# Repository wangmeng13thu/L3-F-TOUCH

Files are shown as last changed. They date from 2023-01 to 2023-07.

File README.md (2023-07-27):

L3 F-TOUCH Design
=================

<p align="center">
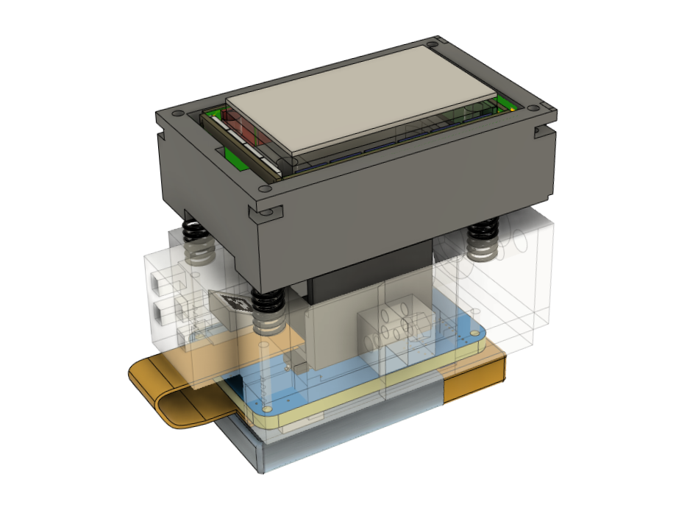
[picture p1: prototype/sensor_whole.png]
  
</p>

L3 F-TOUCH sensor is an enhanced version of the GelSight sensor, it acquires a much better three-axis force sensing capability while being ***L***ight-weight, ***L***ow-cost and wire***L***ess for the ease of replication and deployment.

We decouple the three-axis force and tactile information using a suspension structure with mirrored visual tag. The L3 F-TOUCH demonstrates an improved force sensing capability immuned from contact geometry compared to other GelSight-like designs while being light and cost-effective compared to commercial three-axis force sensors. The wireless data transmission feature also enables broader applications of akin vision-based tactile sensors. 

This repository contains the documentation and manufacturing files for L3 F-TOUCH tactile sensor.

Manufacturing
-------------

* The 3D design files and BOM are in [prototype](prototype/);
* The wireless camera module design is in [PCB](PCB/);

Running
-----------

* Compile and upload the [firmware](/firmware) via [PlatformIO](https://github.com/platformio/platformio-vscode-ide) (WiFi must be configured);
* Use [VLC](https://github.com/videolan/vlc) to check the RTSP video streaming. Adress can be found in Serial monitor when startup.
* Run [L3-FTOUCH.py](/software/L3-FTOUCH.py) for demonstration;

Remarks
-----------
* Modify the firmware to use picture mode for higher quality images (advanced).

Video
-----------

L3 F-TOUCH: A Wireless GelSight with Decoupled Tactile and Three-axis Force Sensing (https://www.youtube.com/watch?v=NIsbJhs_ChQ "L3 F-TOUCH: A Wireless GelSight with Decoupled Tactile and Three-axis Force Sensing")

Citation
-----------
If you use this project in your research, please cite:

```BibTeX
@article{li20233,
  title={L$^3$ F-TOUCH: A Wireless GelSight with Decoupled Tactile and Three-axis Force Sensing},
  author={Li, Wanlin and Wang, Meng and Li, Jiarui and Su, Yao and Jha, Devesh K and Qian, Xinyuan and Althoefer, Kaspar and Liu, Hangxin},
  journal={IEEE Robotics and Automation Letters},
  volume={8},
  number={8},
  pages={5148--5155},
  year={2023},
  publisher={IEEE}
}
```

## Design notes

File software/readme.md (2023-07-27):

<p align="left">
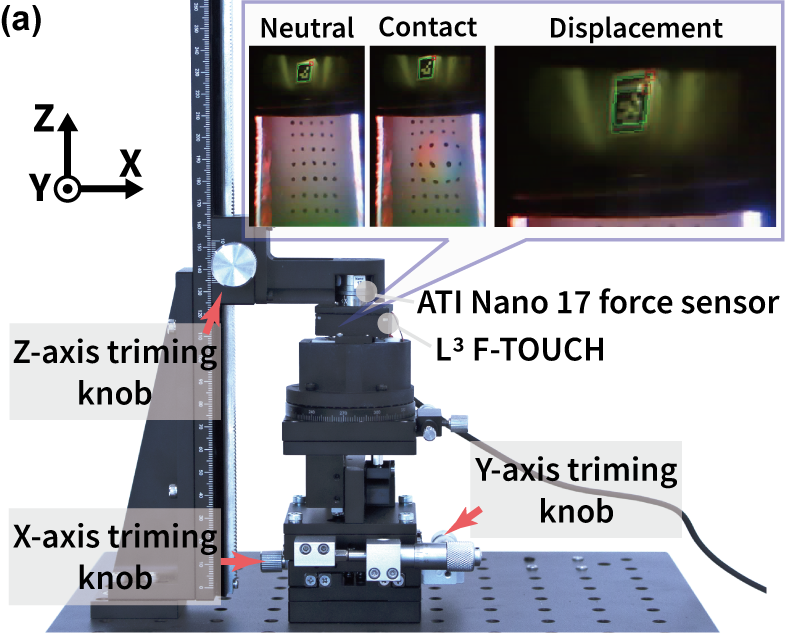
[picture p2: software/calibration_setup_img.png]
  
</p>

* For the Tactile Mode, you can use any vision-based tactile sensor (VBTS) technique, for instance, GelSight, GelSlim etc.
* For the Force Mode, you can also use any AR tag. Here we use ArUco marker and collected the groundtruth data from the ATI F/T sensor and the L3-FTOUCH sensor data using the setup shown above. Please make sure that the two data are synchronized and saved, for instance, in a csv file. Then run ForceCalibration3by3.py to generate the calibration matrix forcematrix.npy. An example of the predicted data is presented in Linearity.mat. The complete version with user interface is L3-FTOUCH.py.

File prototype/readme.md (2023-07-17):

This page is for the sensor's prototype components:

* files with .stl are 3D printed sensor sturctures. The Top is connected to the Bottom1 and Bottom2 via springs, while Bottom1 and Bottom2 are connected via bolts.

* The SMD LEDs used are LUXEON 2835 Color Line. The PCB of the LEDs are in [PCB](../PCB/) folder.

* The Marker used is ArUco Marker 4x4(50) which can be generated from [here](https://chev.me/arucogen/).

* The BOM is as follows:
<p align="left">
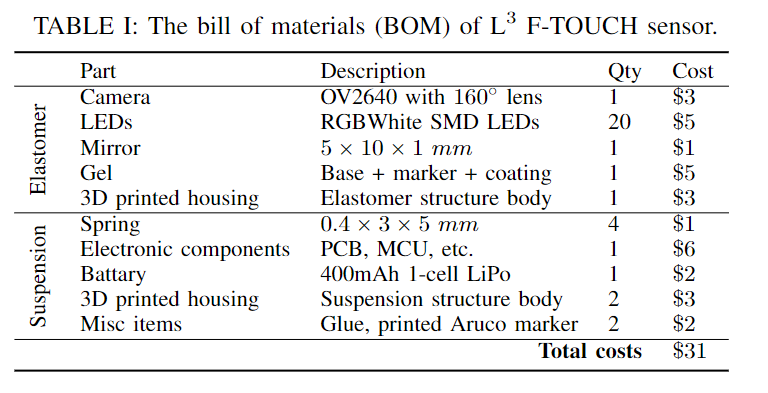
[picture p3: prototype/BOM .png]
  
</p>

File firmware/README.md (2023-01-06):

# GelSightRTSP

This repository is based on [ESP32-CAM RTSP stream](https://github.com/circuitrocks/ESP32-RTSP), with more functions added and optimized for GelSight sensors. 

## Compiling with PlatformIO
Just open the folder containing the files with PlatformIO and adjust your settings in platformio.ini. Required libraries are either automatically installed or in the lib folder.

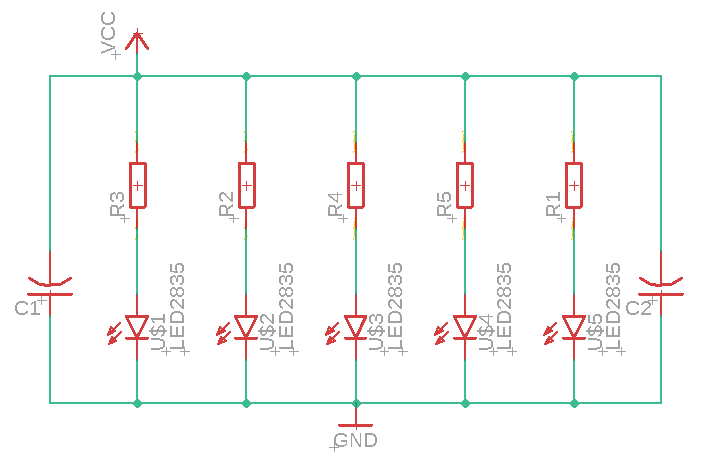
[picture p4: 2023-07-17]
PCB/PCB_Schematic.png

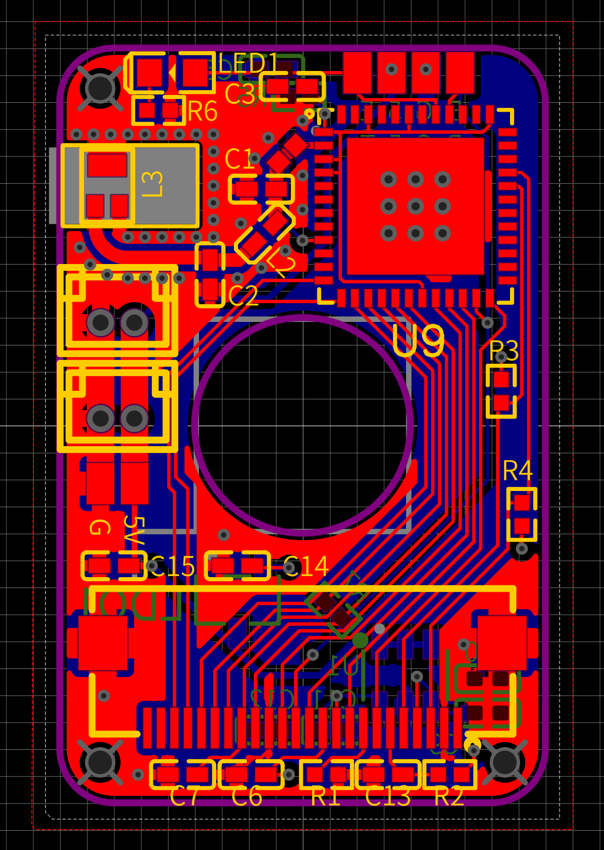
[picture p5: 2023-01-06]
PCB/pcb.png

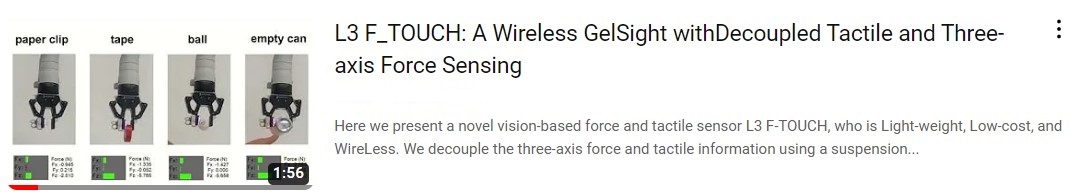
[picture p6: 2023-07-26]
prototype/YouTube.jpg

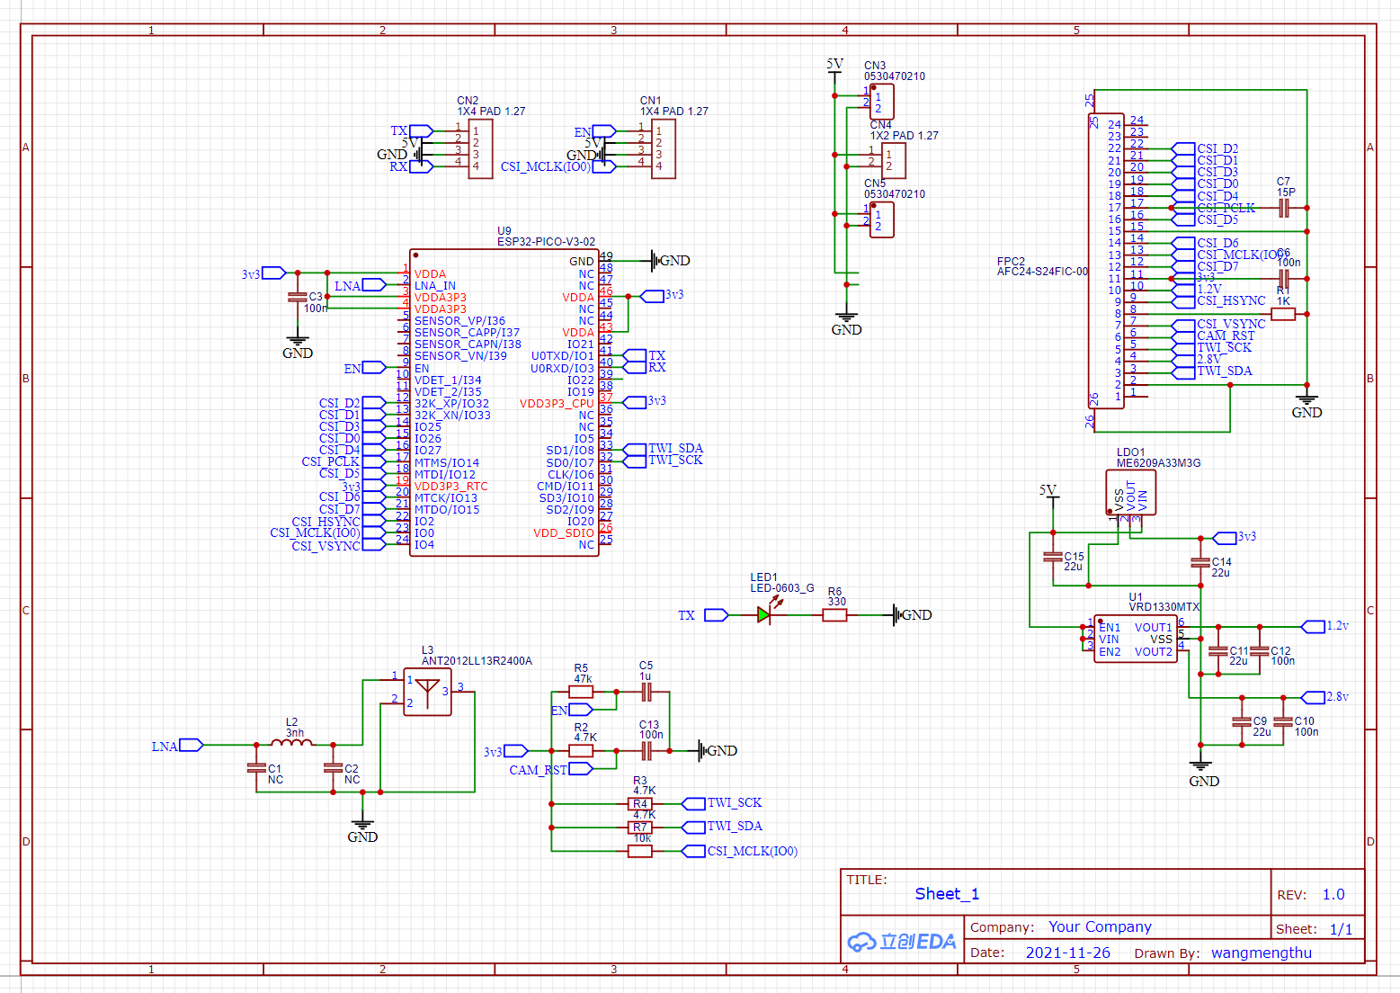
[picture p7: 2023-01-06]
PCB/scheme.png

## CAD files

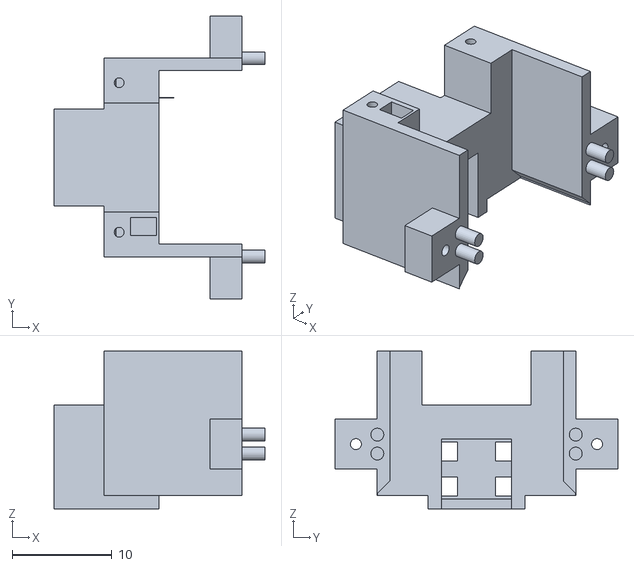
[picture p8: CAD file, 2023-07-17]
prototype/Bottom1.stl
21.1 x 28.4 x 15.8

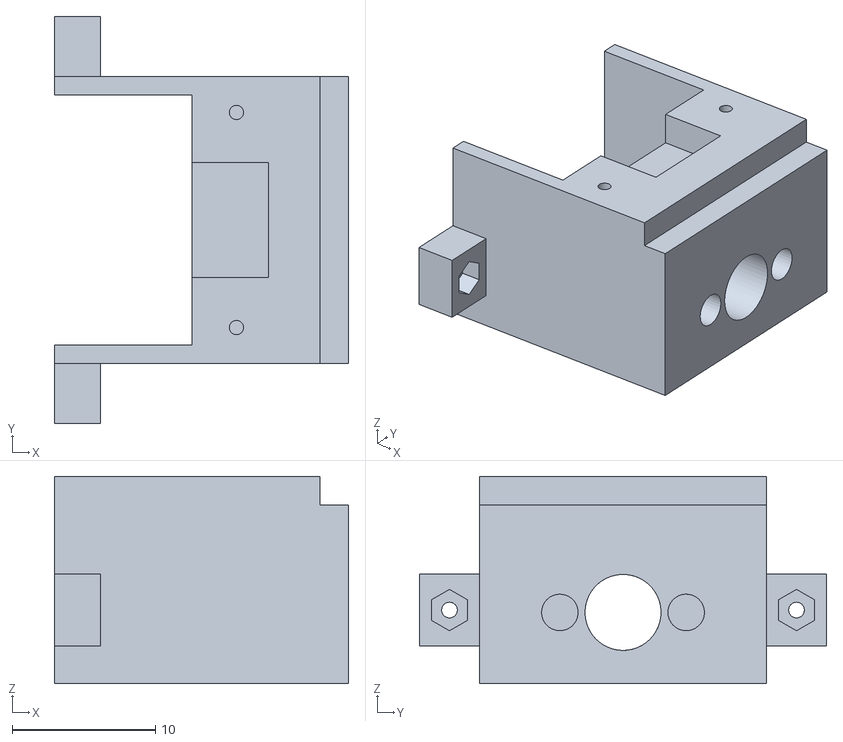
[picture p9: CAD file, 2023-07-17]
prototype/Bottom2.stl
20.5 x 28.4 x 14.5

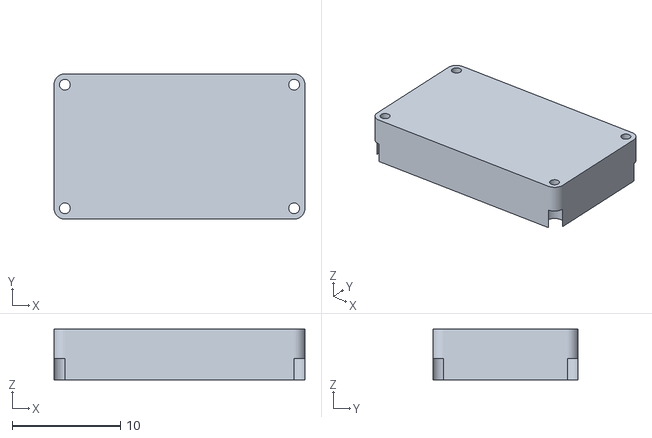
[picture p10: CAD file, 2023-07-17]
prototype/Acrylicsheet.stl
23.2 x 13.4 x 4.70

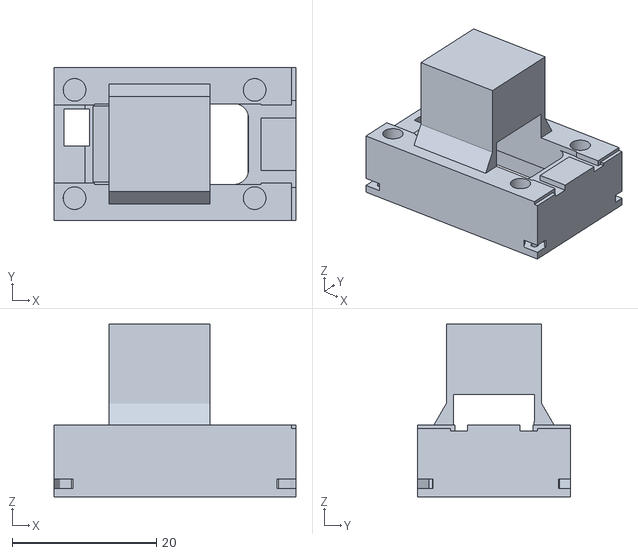
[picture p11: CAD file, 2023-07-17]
prototype/Top.stl
33.5 x 21.2 x 24.0

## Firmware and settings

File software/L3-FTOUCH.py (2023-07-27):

import numpy as np
import cv2
import sys
# from utils import ARUCO_DICT
import argparse
import time
import math
import matplotlib.pyplot as plt
import threading
import nidaqmx
import tkinter as tk
import csv
from PIL import Image, ImageTk
import imutils
import pandas as pd
import torch
import torch.nn as nn
from torch.utils.data import Dataset, DataLoader

# sys.path.append('TestWifiCamera/GelForce')
import setting_GelForce
from lib import find_marker
from collections import deque
from fast_poisson import fast_poisson
from fast_poisson1 import poisson_reconstruct



class Processing:
    def __init__(self, vs, aruco_dict_type):
        self.vs = vs
        self.aruco_dict_type = aruco_dict_type
        self.frame = None
        self.frame_Gel = None
        self.thread1 = None
        self.thread2 = None
        self.stopEvent = None
        self.writedata = False
        self.resetsensor = False
        self.counter = 0
        self.scale = 1

        self.ab_array = np.load('./correction.npz')
        self.x_index = self.ab_array['x']
        self.y_index = self.ab_array['y']
        self.FT_Cali = np.zeros((6,6))

        self.cameraMatrix = np.float32([[160.1881, 0, 247.7054],
                                        [0, 160.3019, 170.0790],
                                        [0, 0, 1.0]])

        self.Sensor_Cali = np.load('./forcematrix.npy')
        # self.Sensor_Cali = np.float32([[625.5201, 110.8314, -532.1205],
        #                                [203.4257, -993.7571, -671.1609],
        #                                [-1492.8, 112.8753, 5734.2]])

        self.disCoeffs = np.float32([0.2616 , -0.2155, 0.0032, 0.0022, 0.0226])

        self.ATIdata = np.zeros((6,1))
        self.FT = {'Fx': 0.0, 'Fy': 0.0, 'Fz': 0.0, 'Tx': 0.0, 'Ty': 0.0, 'Tz': 0.0}
        self.ati_bias = np.zeros((6, 1))
        self.sensor_bias = np.zeros((3, 1))
        self.tvec = np.zeros((3, 1))
        self.pre_tvec = np.zeros((3, 1))
        self.tvecFT = np.zeros((3, 1))
        self.idcheck = True


        self.FrameGel_inix = 185
        self.FrameGel_iniy = 35
        self.FrameGel_width = 120
        self.FrameGel_height = 160
        self.con_flag1 = True
        self.reset_shape1 = True
        self.restart1 = False
        self.refresh1 = False
        self.writeTacdata = False
        self.slip_indicator1 = False
        self.slip_indicator2 = False
        # abe_array = np.load('abe_corr.npz')
        # self.x_index = abe_array['x']
        # self.y_index = abe_array['y']

        self.collideThre = 3    # 2.5
        self.collide_rotation = 4.
        self.showimage1 = True
        self.showimage2 = False
        self.data1 = deque(maxlen=75)
        self.collision_detected = False
        self.slip = True
        self.rotateslip = True
        self.calibrate1 = False
        self.taccount = 110

        self.table = np.load('./table_smooth.npy')
        self.zeropts_scale_bin = np.load('./zeropts_scale_bin.npy')
        # self.zeropoint =  [-55, -30, -55]
        # self.lookscale = [120., 60., 120.]
        # self.bin_num = [60, 60, 60]
        self.zeropoint = self.zeropts_scale_bin[0]
        self.lookscale = self.zeropts_scale_bin[1]
        self.bin_num = self.zeropts_scale_bin[2]

        self.useTable = True
        self.useMLP = False
        self.useMask = True

        self.root = tk.Tk()
        canvas = tk.Canvas(self.root, height=640, width=960, bg='gray')
        canvas.pack()
        self.panel1 = None
        self.panel2 = None
        self.panel3 = None
        self.label1 = None
        self.label2 = None

        button1 = tk.Button(canvas, height=2, width=6, text="Start", font=("Times", 20), bg='white', command=self.startsensor)
        button1.place(relx=0.05, rely=0.01, relwidth=0.25, relheight=0.05)
        button2 = tk.Button(canvas, height=2, width=6, text="Record", font=("Times", 20), bg='white', command=self.plotdata)
        button2.place(relx=0.375, rely=0.01, relwidth=0.25, relheight=0.05)
        button3 = tk.Button(canvas, height=2, width=6, text="Quit", font=("Times", 20), bg='white', command=self.quitsensor)
        button3.place(relx=0.7, rely=0.01, relwidth=0.25, relheight=0.05)

        self.panel1 = tk.Label(canvas)
        self.panel1.place(relx=0.05, rely=0.1, relwidth=0.2, relheight=0.3)    #0.08 0.3 0.5
        self.panel2 = tk.Label(canvas)
        self.panel2.place(relx=0.35, rely=0.1, relwidth=0.2, relheight=0.3)    #0.08 0.3 0.5
        self.panel3 = tk.Label(canvas)
        self.panel3.place(relx=0.65, rely=0.1, relwidth=0.2, relheight=0.3)  # 0.08 0.3 0.5

        self.label1 = tk.Label(canvas, height=2, width=18, bg='white')
        self.label1.place(relx=0.05, rely=0.55, relwidth=0.65, relheight=0.3)
        self.label2 = tk.Label(canvas, height=2, width=18, bg='white', font=("Arial", 12))
        self.label2.place(relx=0.75, rely=0.55, relwidth=0.2, relheight=0.3)
        #self.task = None


        self.stopEvent = threading.Event()
        self.thread1 = threading.Thread(target=self.videoloop, args=())
        print("start threading1")
        self.thread1.start()

        # self.thread2 = threading.Thread(target=self.atiloop, args=())
        # print("start threading2")
        # self.thread2.start()
        #
        # self.root.mainloop()

        self.root.wm_title("Force/Tactile Sensor")
        self.root.wm_protocol("WM_DELETE_WINDOW", self.onclose)

    def atiloop(self):
        with nidaqmx.Task() as task:
            task.ai_channels.add_ai_voltage_chan("Dev2/ai0:5")
            while True:
                self.ATIdata = task.read(number_of_samples_per_channel=1)
                self.ATIdata = np.array(self.ATIdata)


    def pose_esitmation(self, frame, aruco_dict_type):
        gray = cv2.cvtColor(frame, cv2.COLOR_BGR2GRAY)
        cv2.aruco_dict = cv2.aruco.Dictionary_get(aruco_dict_type)
        parameters = cv2.aruco.DetectorParameters_create()

        corners, ids, rejected_img_points = cv2.aruco.detectMarkers(gray, cv2.aruco_dict, parameters=parameters, cameraMatrix=self.cameraMatrix,
                                                                    distCoeff=self.disCoeffs)
        # print(f"ids are {ids}")
        # If markers are detected
        if len(corners) > 0 and ids[0] == [0] and len(ids) == 1:
            rvec, tvec, markerPoints = cv2.aruco.estimatePoseSingleMarkers(corners, 0.003, self.cameraMatrix, self.disCoeffs)
                # Draw a square around the markers
            cv2.aruco.drawDetectedMarkers(frame, corners)

                # Draw Axis
            cv2.aruco.drawAxis(frame, self.cameraMatrix, self.disCoeffs, rvec, tvec, 0.002)

            self.tvec = tvec[:, :, [1, 0, 2]]
            self.tvec = self.tvec.reshape(3, 1)
            self.tvec[1,:] *= -1
            self.pre_tvec = self.tvec.copy()

        if ids is None:
            self.idcheck = False
        else:
            self.idcheck = True
                # print(f"tvec OG is {tvec} and OG shape is {tvec.shape}")
                # # print(f"tvec1 is {tvec1} and 1 shape is {tvec1.shape}")
                # print(f"tvec self is {self.tvec} and self shape is {self.tvec.shape}")

        return frame

    def make_kernel(self, n, k_type):
        if k_type == 'circle':
            kernal = cv2.getStructuringElement(cv2.MORPH_ELLIPSE, (n, n))
        else:
            kernal = cv2.getStructuringElement(cv2.MORPH_RECT, (n, n))
        return kernal

    def marker_detection(self, raw_image):
        m, n = raw_image.shape[1], raw_image.shape[0]
        # raw_image = cv2.pyrDown(raw_image).astype(np.float32)
        raw_image_blur = cv2.GaussianBlur(raw_image.astype(np.float32), (3, 3), 0).astype(np.uint8)
        ref_blur = cv2.GaussianBlur(raw_image.astype(np.float32), (25, 25), 0).astype(np.uint8)

        diff = cv2.subtract(ref_blur, raw_image_blur)
        # diff = raw_image_blur - ref_blur
        diff *= 16

        diff[diff < 0] = 0
        diff[diff > 255] = 255

        mask = ((diff[:, :, 0] > 25) & (diff[:, :, 2] > 25) &
                (diff[:, :, 1] > 120)).astype(np.uint8)
        mask *= 255
        # mask = cv2.resize(mask.astype(np.uint8), (m, n))
        mask = cv2.dilate(mask, self.kernel2, iterations=1)
        mask = cv2.erode(mask, self.kernel2, iterations=1)
        mask = cv2.bitwise_not(mask)

        return mask

    def creat_mask_2(self, raw_image, dmask):
        # t = time.time()
        scale = 2
        m, n = raw_image.shape[1], raw_image.shape[0]
        raw_image = cv2.pyrDown(raw_image).astype(np.float32)
        blur = cv2.GaussianBlur(raw_image, (15, 15), 0)
        blur2 = cv2.GaussianBlur(raw_image, (3, 3), 0)
        # print(time.time() - t)
        diff = blur - blur2
        # diff = cv2.resize(diff, (int(m / scale), int(n / scale)))
        # diff = (diff - np.min(diff)) / (np.max(diff) - np.min(diff)) * 255
        diff *= 15.0
        # cv2.imshow('blur2', blur.astype(np.uint8))
        # cv2.waitKey(1)

        diff[diff < 0.] = 0.
        diff[diff > 255.] = 255.

        # diff = cv2.GaussianBlur(diff, (5, 5), 0)
        # cv2.imshow('diff', diff.astype(np.uint8))
        # cv2.waitKey(1)
        mask_b = diff[:, :, 0] > 150
        mask_g = diff[:, :, 1] > 150
        mask_r = diff[:, :, 2] > 150

        mask = ((mask_b * mask_g) + (mask_b * mask_r) + (mask_g * mask_r)) > 0
        # cv2.imshow('mask', mask.astype(np.uint8) * 255)
        # cv2.waitKey(1)
        mask = cv2.resize(mask.astype(np.uint8), (m, n))
        mask = mask * dmask
        kernal4 = self.make_kernel(3, 'circle')
        mask = cv2.dilate(mask, kernal4, iterations=1)
        # cv2.imshow('diff', diff.astype(np.uint8))
        # cv2.imshow('mask', mask.astype(np.uint8) * 255)
        # cv2.waitKey(1)
        # mask = cv2.erode(mask, self.kernal4, iterations=1)
        # print(time.time() - t)
        return (1 - mask) * 255

    def find_dots(self, binary_image):
        # down_image = cv2.resize(binary_image, None, fx=2, fy=2)
        params = cv2.SimpleBlobDetector_Params()
        # Change thresholds
        params.thresholdStep = 5    #0
        params.minThreshold = 1     # 1
        params.maxThreshold = 120    # 40
        params.minDistBetweenBlobs = 9  #9
        params.filterByArea = True
        params.minArea = 12  # 9
        params.maxArea = 1000
        params.filterByCircularity = False
        params.filterByConvexity = False
        params.filterByInertia = False
        params.minInertiaRatio = 0.5 #0.5
        detector = cv2.SimpleBlobDetector_create(params)
        keypoints = detector.detect(binary_image.astype(np.uint8))

        return keypoints

    def make_mask(self, img, keypoints):
        img = np.zeros_like(img[:, :, 0])
        for i in range(len(keypoints)):
            # cv2.circle(img, (int(keypoints[i].pt[0]), int(keypoints[i].pt[1])), 6, (1), -1)
            cv2.ellipse(img,
                        (int(keypoints[i].pt[0]), int(keypoints[i].pt[1])),
                        (8, 6), 0, 0, 360, (255), -1)  #original 10,8
        # cv2.imshow("makemask", img)
        return img

    def rgb2gray(self, rgb):
        return np.dot(rgb[..., :3], [0.33, 0.33, 0.34])

    def defect_mask(self, im_cal):
        # mask = np.load('./TacData_fill/defect_mask.npy')
        # pad, var0, var1, var2, var3 = int(mask[0]), int(mask[1]), int(mask[2]), int(mask[3]), int(mask[4])
        pad = 1
        var0 = 15  # left up 60
        var1 = 15  # right up 60
        var2 = 15  # right down 65
        var3 = 15  # left down 60
        im_mask = np.ones((im_cal.shape))
        triangle0 = np.array([[0, 0], [var0, 0], [0, var0]])
        triangle1 = np.array([[im_mask.shape[1] - var1, 0],
                              [im_mask.shape[1], 0], [im_mask.shape[1], var1]])
        triangle2 = np.array([[im_mask.shape[1] - var2, im_mask.shape[0]], [im_mask.shape[1], im_mask.shape[0]],
                              [im_mask.shape[1], im_mask.shape[0] - var2]])
        triangle3 = np.array([[0, im_mask.shape[0]],
                              [0, im_mask.shape[0] - var3],
                              [var3, im_mask.shape[0]]])
        color = [0]  # im_mask
        cv2.fillConvexPoly(im_mask, triangle0, color)
        cv2.fillConvexPoly(im_mask, triangle1, color)
        cv2.fillConvexPoly(im_mask, triangle2, color)
        cv2.fillConvexPoly(im_mask, triangle3, color)
        im_mask[:pad, :] = 0
        im_mask[-pad:, :] = 0
        im_mask[:, :pad] = 0
        im_mask[:, -pad:] = 0
        return im_mask

    def defect_mask_diff(self, im_cal):
        mask = np.load('./TacData_fill/defect_mask.npy')
        pad, var0, var1, var2, var3 = int(mask[0]), int(mask[1]), int(mask[2]), int(mask[3]), int(mask[4])
        im_mask = im_cal.copy()
        triangle0 = np.array([[0, 0], [var0, 0], [0, var0]])
        triangle1 = np.array([[im_mask.shape[1] - var1, 0],
                              [im_mask.shape[1], 0], [im_mask.shape[1], var1]])
        triangle2 = np.array([[im_mask.shape[1] - var2, im_mask.shape[0]], [im_mask.shape[1], im_mask.shape[0]],
                              [im_mask.shape[1], im_mask.shape[0] - var2]])
        triangle3 = np.array([[0, im_mask.shape[0]],
                              [0, im_mask.shape[0] - var3],
                              [var3, im_mask.shape[0]]])
        color = [0]  # im_mask
        cv2.fillConvexPoly(im_mask, triangle0, color)
        cv2.fillConvexPoly(im_mask, triangle1, color)
        cv2.fillConvexPoly(im_mask, triangle2, color)
        cv2.fillConvexPoly(im_mask, triangle3, color)
        im_mask[:pad, :] = 0
        im_mask[-pad:, :] = 0
        im_mask[:, :pad] = 0
        im_mask[:, -pad:] = 0
        return im_mask

    def defect_mask0(img):
        im_mask = np.ones((img.shape))

        return im_mask.astype(int)

    def sortkeypoints(self, keypoints):
        x, y, xy = [], [], []
        # print(f"keypoint size is {len(keypoints)}")
        for i in range(len(keypoints)):
            x.append(keypoints[i].pt[0])
            y.append(keypoints[i].pt[1])
            xy.append((int(keypoints[i].pt[0]), int(keypoints[i].pt[1])))
        # xy = sorted(xy)
        # xy = sorted(xy, key=lambda x : x[1])
        xy = sorted(xy, key=lambda x: [x[1], x[0]])
        # xy_array = []
        # temp = []
        # for i in range(len(xy)):
        #     xy_array.append(i)
        # print("xy_array is", xy)
        # print("len of xy_array is", len(xy_array))
        return xy

    def draw_flow(self, frame, flow):
        Ox, Oy, Cx, Cy, Occupied = flow
        K = 0
        for i in range(len(Ox)):
            for j in range(len(Ox[i])):
                pt1 = (int(Ox[i][j]), int(Oy[i][j]))
                pt2 = (int(Cx[i][j] + K * (Cx[i][j] - Ox[i][j])), int(Cy[i][j] + K * (Cy[i][j] - Oy[i][j])))
                color = (255, 255, 0)
                if Occupied[i][j] <= -1:
                    color = (127, 127, 255)
                cv2.arrowedLine(frame, pt1, pt2, color, 2, tipLength=0.2)

    def flow_calculate_global_1(self, keypoints2):

        x2, y2, u, v, x1_paired, y1_paired, x2_paired, y2_paired = [], [], [], [], [], [], [], []
        x1_return, y1_return, x2_return, y2_return, u_return, v_return = [], [], [], [], [], []

        for i in range(len(keypoints2)):
            x2.append(keypoints2[i,0] / self.scale)
            y2.append(keypoints2[i,1] / self.scale)
            # x2.append(keypoints2[i].pt[0] / self.scale)
            # y2.append(keypoints2[i].pt[1] / self.scale)

        x2 = np.array(x2)
        y2 = np.array(y2)

        for i in range(x2.shape[0]):
            distance = list(((np.array(self.x_iniref1) - x2[i]) ** 2 +
                             (np.array(self.y_iniref1) - y2[i]) ** 2))
            if len(distance) == 0:
                break
            min_index = distance.index(min(distance))
            u_temp = x2[i] - self.x_iniref1[min_index]
            v_temp = y2[i] - self.y_iniref1[min_index]
            shift_length = np.sqrt(u_temp ** 2 + v_temp ** 2)
            # print 'length',shift_length
            if shift_length < 12:
                x1_paired.append(self.x_iniref1[min_index] -
                                 self.u_addon1[min_index])
                y1_paired.append(self.y_iniref1[min_index] -
                                 self.v_addon1[min_index])
                x2_paired.append(x2[i])
                y2_paired.append(y2[i])
                u.append(u_temp + self.u_addon1[min_index])
                v.append(v_temp + self.v_addon1[min_index])

                del self.x_iniref1[min_index], self.y_iniref1[
                    min_index], self.u_addon1[min_index], self.v_addon1[
                    min_index]

        x1_return = np.array(x1_paired)
        y1_return = np.array(y1_paired)
        x2_return = np.array(x2_paired)
        y2_return = np.array(y2_paired)
        u_return = np.array(u)
        v_return = np.array(v)
        self.x_iniref1 = list(x2_paired)
        self.y_iniref1 = list(y2_paired)
        self.u_addon1 = list(u)
        self.v_addon1 = list(v)

        return x1_return, y1_return, x2_return, y2_return, u_return, v_return

    def flow_calculate_in_contact_1(self, keypoints2):

        x2, y2, u, v, x1_paired, y1_paired, x2_paired, y2_paired = [], [], [], [], [], [], [], []
        temp_x = list(self.x_iniref1)
        temp_y = list(self.y_iniref1)
        temp_u = list(self.u_addon1)
        temp_v = list(self.v_addon1)

        for i in range(len(keypoints2)):
            x2.append(keypoints2[i,0] / self.scale)
            y2.append(keypoints2[i,1] / self.scale)
            # x2.append(keypoints2[i].pt[0] / self.scale)
            # y2.append(keypoints2[i].pt[1] / self.scale)

        x2 = np.array(x2)
        y2 = np.array(y2)
        refresh = False

        for i in range(x2.shape[0]):

            distance = list(((np.array(temp_x) - x2[i]) ** 2 +
                             (np.array(temp_y) - y2[i]) ** 2))
            if len(distance) == 0:
                break
            min_index = distance.index(min(distance))
            u_temp = x2[i] - temp_x[min_index]
            v_temp = y2[i] - temp_y[min_index]
            shift_length = np.sqrt(u_temp ** 2 + v_temp ** 2)
            # print 'length',shift_length

            if shift_length < 12:   #12
                # print xy2.shape,min_index,len(distance)
                x1_paired.append(temp_x[min_index] - temp_u[min_index])
                y1_paired.append(temp_y[min_index] - temp_v[min_index])
                x2_paired.append(x2[i])
                y2_paired.append(y2[i])
                u.append(u_temp + temp_u[min_index])
                v.append(v_temp + temp_v[min_index])

                del temp_x[min_index], temp_y[min_index], temp_u[
                    min_index], temp_v[min_index]

                if shift_length > 10:   #10
                    refresh = True

        return x1_paired, y1_paired, x2_paired, y2_paired, u, v, refresh

    def flow_calculate_global_2(self, keypoints2):

        x2, y2, u, v, x1_paired, y1_paired, x2_paired, y2_paired = [], [], [], [], [], [], [], []
        x1_return, y1_return, x2_return, y2_return, u_return, v_return = [], [], [], [], [], []

        for i in range(len(keypoints2)):
            x2.append(keypoints2[i,0] / self.scale)
            y2.append(keypoints2[i,1] / self.scale)
            # x2.append(keypoints2[i].pt[0] / self.scale)
            # y2.append(keypoints2[i].pt[1] / self.scale)

        x2 = np.array(x2)
        y2 = np.array(y2)

        for i in range(x2.shape[0]):
            distance = list(((np.array(self.x_iniref2) - x2[i]) ** 2 +
                             (np.array(self.y_iniref2) - y2[i]) ** 2))
            if len(distance) == 0:
                break
            min_index = distance.index(min(distance))
            u_temp = x2[i] - self.x_iniref2[min_index]
            v_temp = y2[i] - self.y_iniref2[min_index]
            shift_length = np.sqrt(u_temp ** 2 + v_temp ** 2)
            # print 'length',shift_length
            if shift_length < 12:
                x1_paired.append(self.x_iniref2[min_index] -
                                 self.u_addon2[min_index])
                y1_paired.append(self.y_iniref2[min_index] -
                                 self.v_addon2[min_index])
                x2_paired.append(x2[i])
                y2_paired.append(y2[i])
                u.append(u_temp + self.u_addon2[min_index])
                v.append(v_temp + self.v_addon2[min_index])

                del self.x_iniref2[min_index], self.y_iniref2[
                    min_index], self.u_addon2[min_index], self.v_addon2[
                    min_index]

        x1_return = np.array(x1_paired)
        y1_return = np.array(y1_paired)
        x2_return = np.array(x2_paired)
        y2_return = np.array(y2_paired)
        u_return = np.array(u)
        v_return = np.array(v)
        self.x_iniref2 = list(x2_paired)
        self.y_iniref2 = list(y2_paired)
        self.u_addon2 = list(u)
        self.v_addon2 = list(v)

        return x1_return, y1_return, x2_return, y2_return, u_return, v_return

    def flow_calculate_in_contact_2(self, keypoints2):

        x2, y2, u, v, x1_paired, y1_paired, x2_paired, y2_paired = [], [], [], [], [], [], [], []
        temp_x = list(self.x_iniref2)
        temp_y = list(self.y_iniref2)
        temp_u = list(self.u_addon2)
        temp_v = list(self.v_addon2)

        for i in range(len(keypoints2)):
            x2.append(keypoints2[i,0] / self.scale)
            y2.append(keypoints2[i,1] / self.scale)
            # x2.append(keypoints2[i].pt[0] / self.scale)
            # y2.append(keypoints2[i].pt[1] / self.scale)

        x2 = np.array(x2)
        y2 = np.array(y2)
        refresh = False

        for i in range(x2.shape[0]):
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

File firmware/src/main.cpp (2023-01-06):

#include "main.h"
#include "wifikeys.h"

#define OTA

//config sensor role
#define ROLE FINGER

#define FINGER 0
#define THUMB_PALM 1
#define TRI_PALM 2
#define DOUBLE_PALM_BOT 3
#define DOUBLE_PALM_TOP 4

const int shutterTime[]={1,110,50,20,20};//finger default is 8,thumb_palm,tri_palm 350,double_palm
/** Camera class */
OV2640 cam;
boolean ota=false;

camera_config_t userCamNew {

    .pin_pwdn = 19, //NC
    .pin_reset = -1,//NC

    .pin_xclk = 0,//MCLK

    .pin_sscb_sda = 8,//TWI SDA
    .pin_sscb_scl = 7,//TWI SCK

    // Note: LED GPIO is apparently 4 not sure where that goes
    // per https://github.com/donny681/ESP32_CAMERA_QR/blob/e4ef44549876457cd841f33a0892c82a71f35358/main/led.c
    .pin_d7 = 15,
    .pin_d6 = 13,
    .pin_d5 = 12,
    .pin_d4 = 27,
    .pin_d3 = 25,
    .pin_d2 = 32,
    .pin_d1 = 33,
    .pin_d0 = 26,
    .pin_vsync = 4,
    .pin_href = 2,//HSYNC
    .pin_pclk = 14,
    .xclk_freq_hz = 24000000, //24000000
    .ledc_timer = LEDC_TIMER_1,
    .ledc_channel = LEDC_CHANNEL_1,


#ifdef USE_PNG
	.pixel_format = PIXFORMAT_RGB565,	
#if ROLE
	.frame_size = FRAMESIZE_VGA,
#else
    .frame_size = FRAMESIZE_VGA,
#endif

#else
	 .pixel_format = PIXFORMAT_JPEG,

#ifdef ENABLE_RTSPSERVER
#if ROLE
	.frame_size = FRAMESIZE_HQVGA,	
#else
    .frame_size = FRAMESIZE_QCIF,
#endif

#else // ENABLE_WEBSERVER
#if ROLE
	.frame_size = FRAMESIZE_HQVGA,
#else
    .frame_size = FRAMESIZE_QCIF,
#endif

#endif
#endif


#ifdef ENABLE_WEBSERVER	
    .jpeg_quality = 3,             //0-63 lower numbers are higher quality	10
    .fb_count = 1 // if more than one i2s runs in continous mode.  Use only with jpeg
#else //enable rtspserver
	.jpeg_quality = 10,             //0-63 lower numbers are higher quality	10
    .fb_count = 2 // if more than one i2s runs in continous mode.  Use only with jpeg
#endif

};

camera_config_t test {

    .pin_pwdn = 32,
    .pin_reset = -1,

    .pin_xclk = 0,

    .pin_sscb_sda = 26,
    .pin_sscb_scl = 27,

    // Note: LED GPIO is apparently 4 not sure where that goes
    // per https://github.com/donny681/ESP32_CAMERA_QR/blob/e4ef44549876457cd841f33a0892c82a71f35358/main/led.c
    .pin_d7 = 35,
    .pin_d6 = 34,
    .pin_d5 = 39,
    .pin_d4 = 36,
    .pin_d3 = 21,
    .pin_d2 = 19,
    .pin_d1 = 18,
    .pin_d0 = 5,
    .pin_vsync = 25,
    .pin_href = 23,
    .pin_pclk = 22,
    .xclk_freq_hz = 24000000,
    .ledc_timer = LEDC_TIMER_1,
    .ledc_channel = LEDC_CHANNEL_1,
    .pixel_format = PIXFORMAT_JPEG,
    // .frame_size = FRAMESIZE_UXGA, // needs 234K of framebuffer space
    // .frame_size = FRAMESIZE_SXGA, // needs 160K for framebuffer
    // .frame_size = FRAMESIZE_VGA, // needs 96K or even smaller FRAMESIZE_SVGA - can work if using only 1 fb
    // .frame_size = FRAMESIZE_QCIF,
 .frame_size = FRAMESIZE_VGA,
    .jpeg_quality = 10,               //0-63 lower numbers are higher quality
    .fb_count = 2 // if more than one i2s runs in continous mode.  Use only with jpeg
};


void setup()
{
	// Start the serial connection
	Serial.begin(115200);

	Serial.println("\n\n##################################");
	Serial.printf("Internal Total heap %d, internal Free Heap %d\n", ESP.getHeapSize(), ESP.getFreeHeap());
	Serial.printf("SPIRam Total heap %d, SPIRam Free Heap %d\n", ESP.getPsramSize(), ESP.getFreePsram());
	Serial.printf("ChipRevision %d, Cpu Freq %d, SDK Version %s\n", ESP.getChipRevision(), ESP.getCpuFreqMHz(), ESP.getSdkVersion());
	Serial.printf("Flash Size %d, Flash Speed %d\n", ESP.getFlashChipSize(), ESP.getFlashChipSpeed());
	Serial.println("##################################\n\n");

	
	delay(100);
	
	
	cam.init(userCamNew);
	delay(100);

	sensor_t * s = esp_camera_sensor_get();
  	// s->set_wb_mode(s, 1);//enable manul WB as sunny
    // s->set_exposure_ctrl(s,0);//enable manul shutter 
    // s->set_saturation(s, 1);  
	// // s->set_sharpness(s, 2);
	// s->set_aec_value(s,shutterTime[ROLE]);//shutter time

    //try adjust WB (seems RGB)
    // s->set_reg(s,0XCC,0xFF,0x52);//R default:0x50 3.50:0x48 3.53:0x48 3.61:0x52 3.60:0x55 3.59:0x48 3.56:0x54 3.68:0x50 3.55:0x53 3.58:0x54 3.63:0x50 3.52:0x54 3.54:0x52 3.62  3.66:0x50 3.51:0x48 3.53:0x52 3.57:0x52 3.61 0x48 3.65:0x48
    // s->set_reg(s,0XCD,0xFF,0x45);//G default:0x41 3.50:0x45 3.53:0x41 3.61:0x45 3.60:0x45 3.59:0x45 3.56:0x45 3.68:0x41 3.55:0x42 3.58:0x44 3.63:0x48 3.52:0x45 3.54:0x41 3.62  3.66:0x45 3.51:0x41 3.53:0x41 3.57:0x45 3.61 0x45 3.65:0x41
    // s->set_reg(s,0XCE,0xFF,0x50);//B default:0x54 3.50:0x52 3.53:0x50 3.61:0x50 3.60:0x54 3.59:0x52 3.56:0x54 3.68:0x42 3.55:0x54 3.58:0x54 3.63:0x52 3.52:0x54 3.54:0x52 3.62  3.66:0x52 3.51:0x50 3.53:0x52 3.57:0x48 3.61 0x52 3.65:0x50

	//top finger default RGB : 0x52 0x45 0x50
	//middle finger default RGB : 0x50 0x42 0x52
	//bottom finger default RGB : 0x46 0x42 0x48
	//TRI_PALM default: 0x46 0x42 0x48

	// Connect the WiFi
    Serial.println("Wifi init start");
	WiFi.mode(WIFI_STA);
	WiFi.begin(ssid, password);
	//WiFi.setTxPower(WIFI_POWER_8_5dBm);
	Serial.println("TX Power: "+String(WiFi.getTxPower()));

	while (WiFi.status() != WL_CONNECTED)
	{
		delay(500);
		Serial.print(".");
	}
	// Print information how to contact the camera server
	IPAddress ip = WiFi.localIP();
	Serial.print("\nWiFi connected with IP ");
	Serial.println(ip);


#ifdef ENABLE_RTSPSERVER
	Serial.print("Stream Link: rtsp://");
	Serial.print(ip);
	Serial.println(":8554/mjpeg/1\n");
	// Initialize the RTSP stream server
	initRTSP();
#endif
#ifdef ENABLE_WEBSERVER
	Serial.print("Browser Stream Link: http://");
	Serial.print(ip);
	Serial.println("\n");
	Serial.print("Browser Single Picture Link: http://");
	Serial.print(ip);
	Serial.println("/jpg\n");
	// Initialize the HTTP web stream server
	initWebStream();
#endif
#ifdef ENABLE_UDPRAW
	Serial.println("Broadcast via UDP, to port 8888");
	initUDPraw();
#endif
#ifdef USE_PNG
	initEncoder();
	s->set_reg(s,0XDA,0x01,0x01); //change high byte first/low byte first of RGB565 data
#endif

	//use RX PIN for OTA 
	pinMode(3,INPUT_PULLUP);
}
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

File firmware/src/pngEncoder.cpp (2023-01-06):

#include "main.h"
#include <PNGenc.h>

#define PNG_BUF 600000
#define COMPRESS_LEVEL 5 // ZLIB compression levels: 1 = fastest, 9 = most compressed (slowest)


PNG png; // static instance of the PNG encoder lass
int size_png;
TaskHandle_t pngTaskHandler;
// Memory to hold the output file
uint8_t* outA;
uint8_t* outB;

uint8_t *buf_png = outA;


void pngTask(void *pvParameters)
{
    while (1)
    {
        // while(transing_png)
        //     vTaskDelay(1);

        camera_fb_t *fb = esp_camera_fb_get();
        uint8_t *buf = fb->buf;
        int WIDTH = fb->width;
        int HEIGHT = fb->height;

        int time_ms = millis();
        uint8_t* writeBuf = buf_png==outA?outB:outA;

        
        int rc = png.open(writeBuf, PNG_BUF);
        if (rc == PNG_SUCCESS)
        {

            rc = png.encodeBegin(WIDTH, HEIGHT, PNG_PIXEL_TRUECOLOR, 3*8, NULL, COMPRESS_LEVEL); //Bpp: bits per pixel

            if (rc == PNG_SUCCESS)
            {
                uint8_t tempLine[WIDTH * 3];
                for (int y = 0; y < HEIGHT && rc == PNG_SUCCESS; y++)
                {     
                    rc = png.addRGB565Line(( uint16_t*)buf,tempLine);
                    //Serial.println(rc);
                    buf += WIDTH * 2;
                } // for y
                size_png = png.close();
                while(transing_png)
                    vTaskDelay(1);
                buf_png = writeBuf;


                Serial.printf("%d bytes of data written to file in %d ms\n", size_png, millis() - time_ms);
            }
        }

        esp_camera_fb_return(fb);

        vTaskDelay(1);
    }
}

void initEncoder()
{
    outA = (uint8_t* )ps_malloc(PNG_BUF);
    outB = (uint8_t* )ps_malloc(PNG_BUF);
    xTaskCreatePinnedToCore(pngTask, "PNG", 4000, NULL, tskIDLE_PRIORITY+1, &pngTaskHandler,1);
}

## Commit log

2022-10-14 add udpraw
    [ESP32-CAM-Back.stl, ESP32-CAM-Breadboard.fzz, ESP32-CAM-Case.f3z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]
2023-02-13 Rename software/Sensor Output/Readme.md to software/sensor output/Readme.md
